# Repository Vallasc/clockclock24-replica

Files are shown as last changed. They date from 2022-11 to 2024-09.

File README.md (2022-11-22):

# ClockClock 24 Replica
This is my personal implementation of the "ClockClock 24" by [Humans Since 1982](https://www.humanssince1982.com/).

<div align="center">
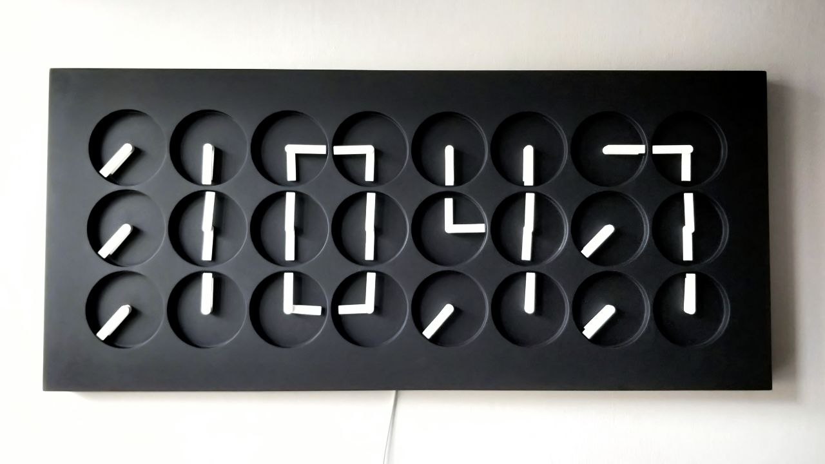
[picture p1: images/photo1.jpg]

</div>

| DISCLAIMER: All files in this repository are intended for personal use only. All design rights go to [Humans Since 1982](https://www.humanssince1982.com/).|
| - |

Clockclock is a kinetic sculpture design by Humans Since 1982, consisting of 24 clocks which by animating show the time in digital format. My attempt to create a replica started by designing the PCB and the case that houses them, and then writing the software to drive the clocks.

---

### Table of Contents: 
1. [Hardware](#hardware)
    1. [Motor](#motor)
    2. [Microcontroller](#microcontroller)
    3. [PCB](#pcb)
2. [Software](#software)
    1. [Master](#master)
    2. [Slave](#slave)
    3. [Web Interface](#web-interface)
    4. [Hands calibration](#hands-calibration)
3. [Case and clock's hands](#case-and-clocks-hands)
4. [Final result](#final-result)

---

## Hardware
The entire clock is composed of 24 sub-clocks, arranged on a 8x3 matrix, that are fully independent. A module that contains 3 clocks and can show vertically an half digit has been designed. A total of 8 boards are used to make up the entire clock, nothing prohibits adding more, thus increasing the number of digits.

### Motor
After careful research, *VID28-05* (or *BKA30D-R5*) stepper motor was chosen. It is made by two separate motors that drive the two shafts individually, that is perfect for attaching the hands. Moreover, this type is sold by some vendors (search on Aliexpress) with no endstops and can turn freely.

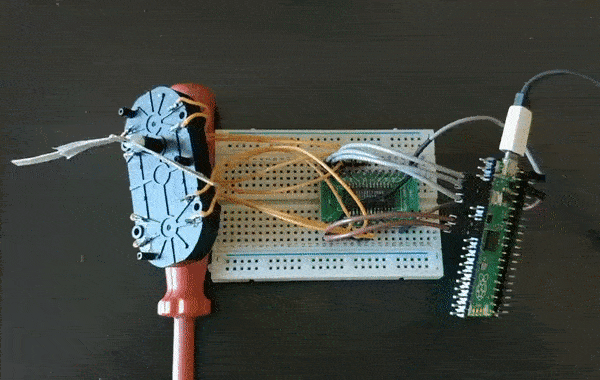
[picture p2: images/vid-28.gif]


These motors are low power and can be runned directly by the microcontroller, but in order not to stress the GPIO a dedicated controller was used. Specifically the *AX1201728SG* (equivalent of *X12.017* and *VID6606* chips) offers advantages over running the motor directly such as uses of microstepping. It requires only two GPIO pins per motor, protects the microprocessor from the inductive effects of the motor coils and requires lower current to be runned by the microcontroller.

### Microcontroller
Two types of microcontrollers are used: **Raspberry-pi-pico** (RP2040) and **ESP8266**. The main reason for this choice is that ESP8266 has wifi capabilities, the design was made before the release of Raspberry-pi-pico-w, now the PCB could be simplified even more. ESP8266 acts as a master and sends commands to the pico boards that run directly the motors. Raspberry-pi-picoIt was chosen because it has a lot of pins, it is reliable and it is available on the market at a relatively low price.

### PCB
The schematic and all the gerber files are placed in the *./pcb* directory. 
<div align="center">
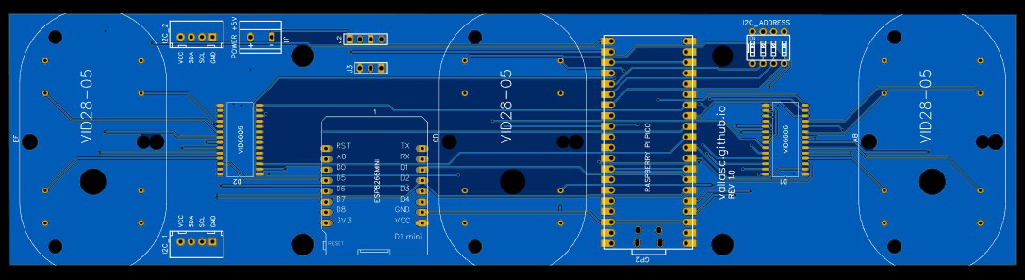
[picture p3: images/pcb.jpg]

</div>

#### Schematic
<div align="center">
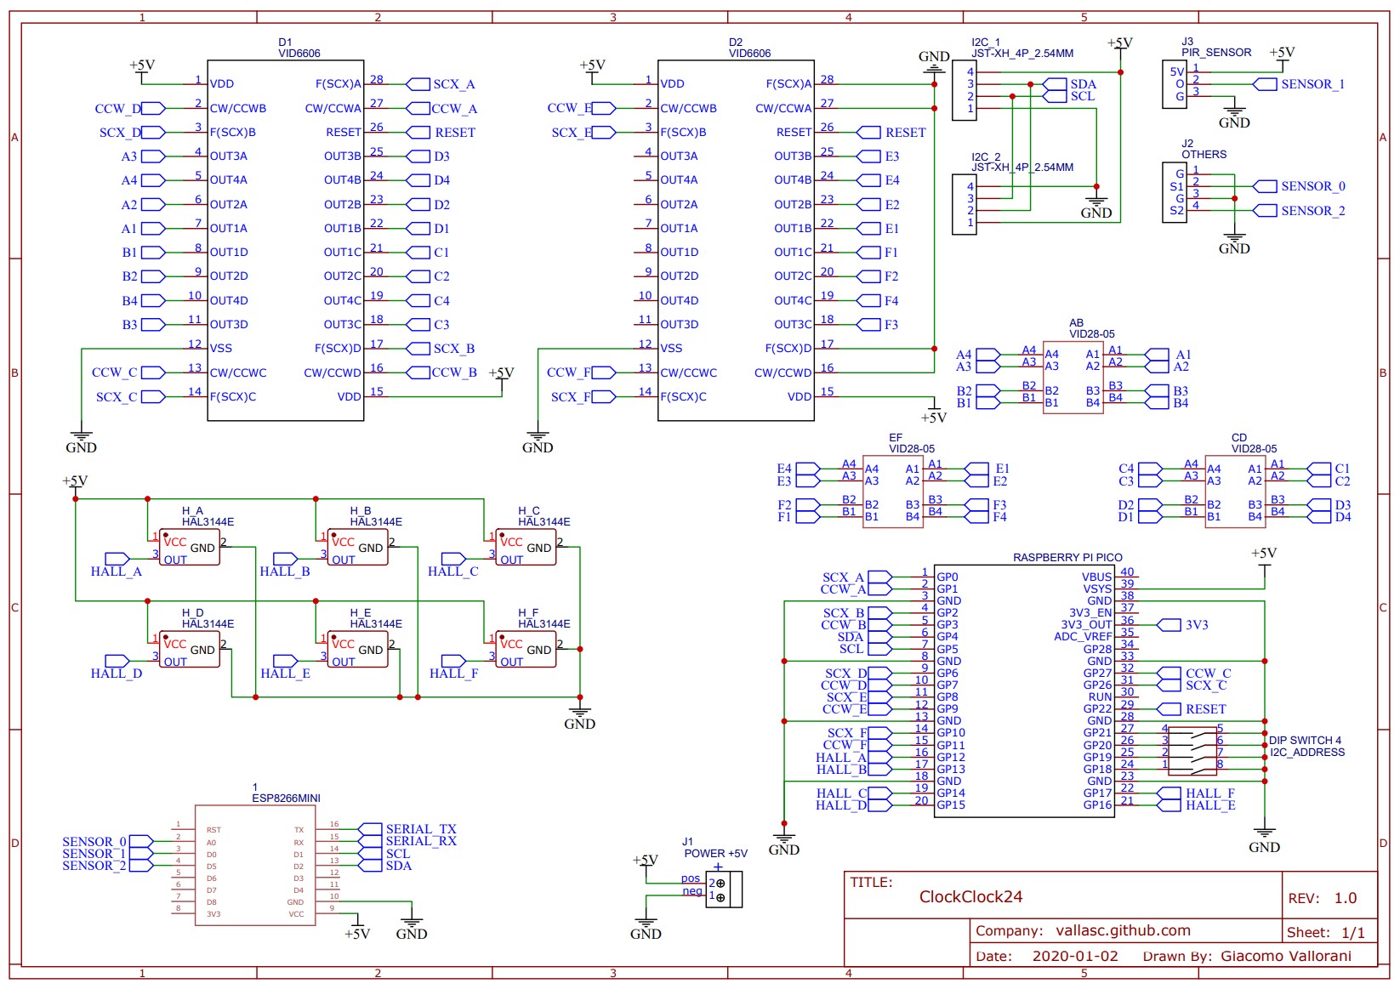
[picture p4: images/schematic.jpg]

</div>
Each board has 2 stepper controllers that in total can run 8 motors. As a design choice, the board has only 3 clocks (6 motors), so 2 outputs are unused. The schematic also contains 6 hall sensors which were to be used to automatically adjust the position of the hands, but in the end they were not added to the final prototype because the magnets were not powerful enough to trigger the sensors. Each board has also housing for ESP8266MINI but it should only be installed on one board (master). This makes it possible to produce only one type of printed circuit board to which components will be soldered according to purpose. Master talks to slaves using I2C protocol, each board is connected to the next in daisy chain. All the boards are powered with 5v and should approximately consume at peak times 1.7 Ah .

#### Bill Of Materials (full clock)
<div align="center">

| Quantity | Name | 
|-|-|
| 8 | PCB board |
| 24 | VID28-05 (or BKA30D-R5) 360 degree mod |
| 16 | AX1201728SG (or VID6606) |
| 8 | Raspberry pi pico |
| 1 | ESP8266 MINI |
| 8 | DIP switch 4 switches |
| 16 | JST XH 2.54 MALE 4 pins |
| 14 | JST XH 2.54 FEMALE 4 pins (for connection cables) |
| 8 | (Optional) power connector |

</div>

---

## Software
On the software side, two different projects were made for master and slave, [PlatformIO](https://platformio.org/)  was used for both of them. The project setup is easy with PlatformIO because it automatically downloads the necessary files. The only parameters you may need to change is *upload_port* and *monitor_port* in *platformio.ini* .

### Slave
The slave code is runned by Raspberry pico, it receives the target hands position through I2C protocol and moves motors accordingly. The I2C address is taken from the position of the 4 switches on the board.

To have a fluid animation, motion must be done using an acceleration curve, so it is used [AccelStepper](http://www.airspayce.com/mikem/arduino/AccelStepper/) library. 
The code is multicore, one core gets bytes from the I2C bus and saves them in the internal buffer, the other core manages to run directly the stepper motors, doing so the animation is not stopped by the I2C interrupts.

### Master
The master code is runned by ESP8266, it is in charge of sending actual hands position to all the boards and to serve the web application.

When powered on, it tries to connect to the configured WiFi network, if it fails then makes an open network. Time synchronization is made, if internet connection is available, using NTP service or it is taken from the client browser that visits the web app. When time changes it sends to the corresponding board the new hands position, the way in which these are to be moved (clockwise, counter clockwise, min distance, max distance, etc.), the speed and the acceleration. In the meantime, it responds to the requests made by the web application made available at http://192.168.1.10 or http://clockclock24.local.

* Animation modes available (for now):
    1. **Lazy**, moves only clock hands that need to be changed by traveling the minimum distance.
    2. **Fun**, moves all the clock's hands in a clockwise direction.
    3. **Waves**, reproduces a domino animation.

### Web interface
On the web application an exact copy of the clock is shown, animations are also cloned and occur at the same time. The interface allows you to change clock mode, set the hours when it should not work and change the wireless connection.

Credits for the clock's web design animation go to [Manuel Wieser](https://manu.ninja/).

<div align="center">
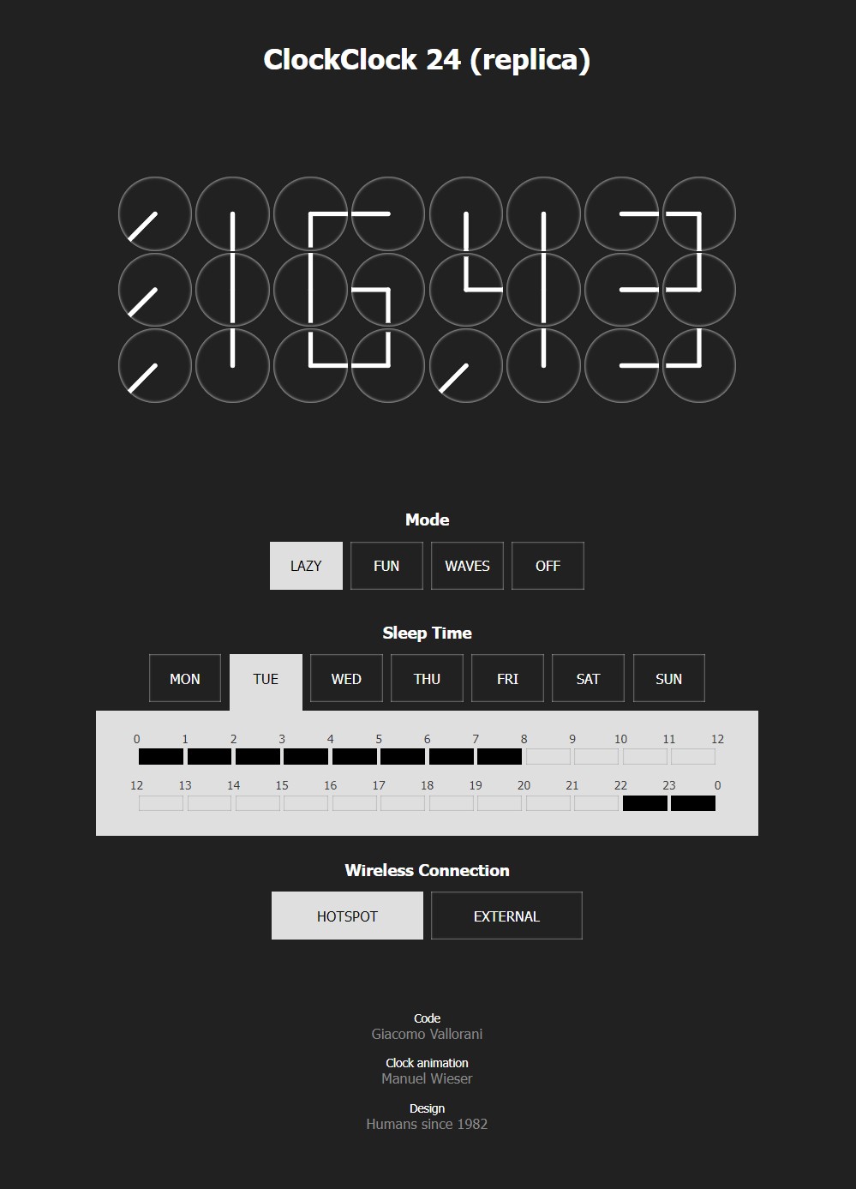
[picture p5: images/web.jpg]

</div>

### Hands calibration
Before powering on the clock, you need to manually set all the clock's hands at 6 o'clock. This process needs to be done every time it is disconnected from power.

---

## Case and clock's hands
The case is one piece, it was made by taking a sheet of black MDF and hollowing out the material with a CNC machine. This gives a lot of stiffness to the structure. The clock's hands are laser cutted from a white plexiglass panel.

Since I don't want to receive a letter from Humans Since 1982’s lawyers, all design files and the actual clock assembly are omitted, more [here](https://hackaday.com/2020/07/31/patent-law-and-the-legality-of-making-something-similar/).
> “Humans Since 1982 have the copyright to works displaying digital time using a grid arrangement of analog clocks…”

---

## Final result
<div align="center">

| Animation type | Result |
| - | - |
| Lazy | sasdasd |
| Fun | sasdasd |
| Waves | sasdasd |

</div>

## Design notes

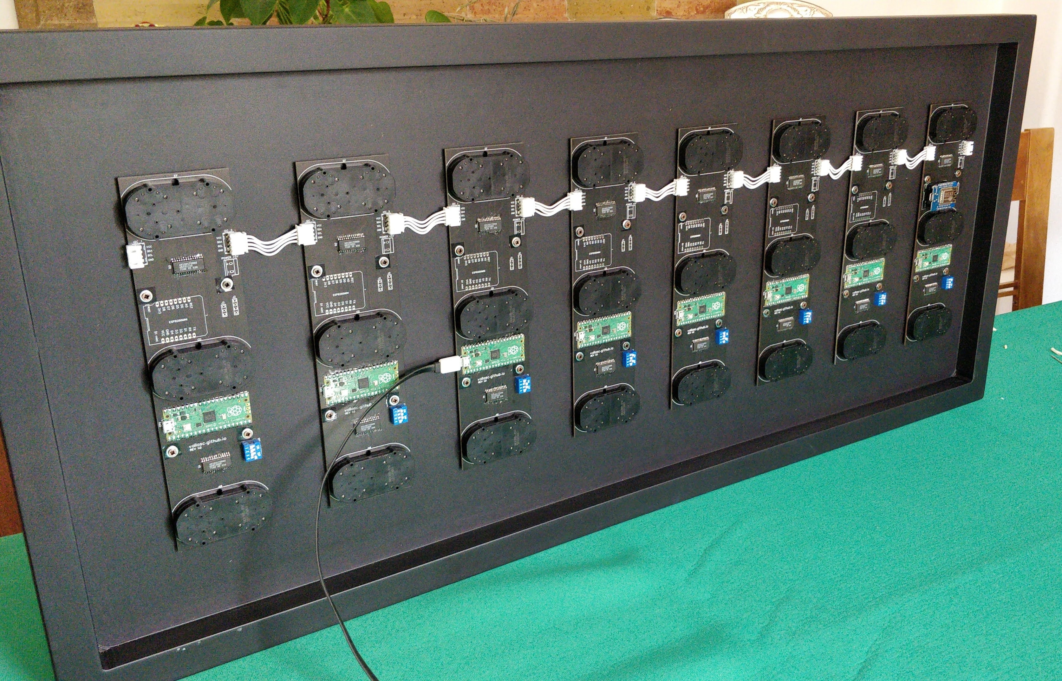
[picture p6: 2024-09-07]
images/IMG-20220928-WA0001.jpeg

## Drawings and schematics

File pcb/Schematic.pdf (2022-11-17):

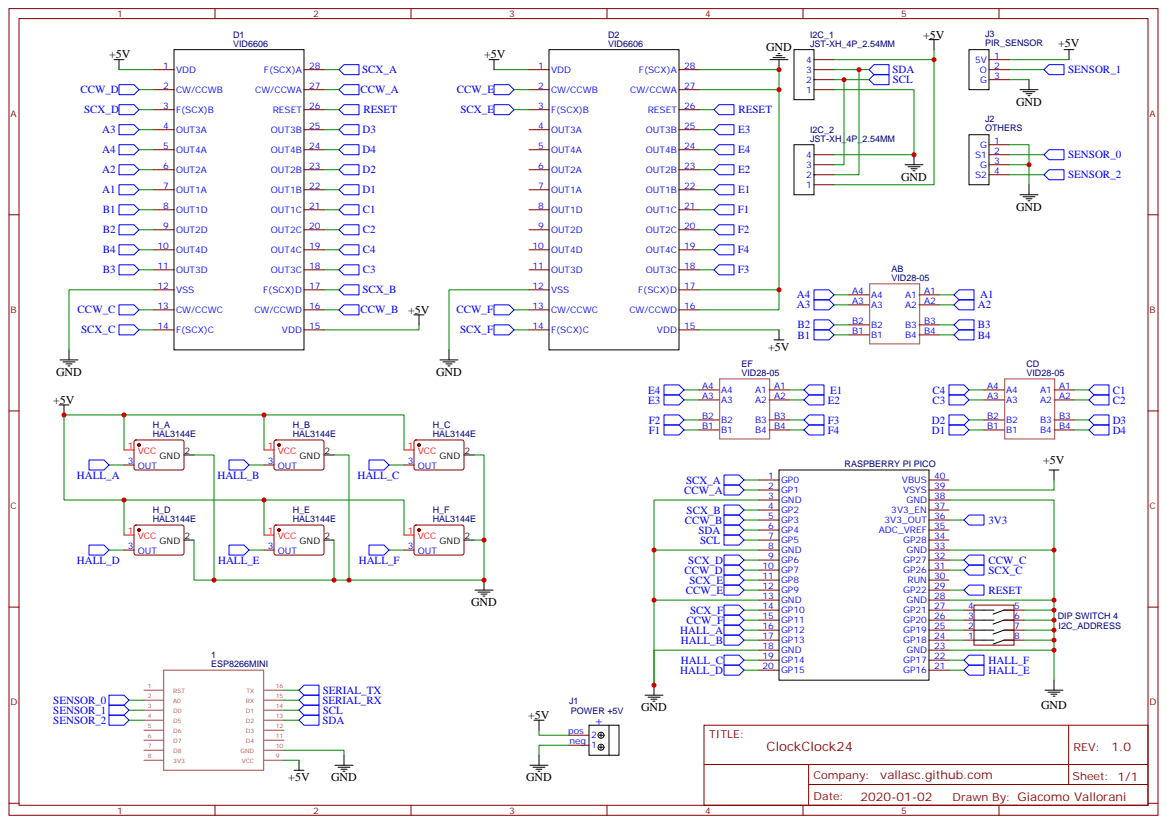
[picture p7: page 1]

Company: vallasc.github.com

Drawn By: Giacomo Vallorani

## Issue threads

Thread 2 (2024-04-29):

Hands turning the incorrect direction.

Kiremas, 2024-04-29:
I finished two PCB's so far which both work but for some reason the hands on some of the steppers turn the wrong way,
which presumably is a fault of the manufacturer of the steppers.

Is there a way to let the slave config know to switch CW and CCW for that particular hand?

Vallasc, 2024-05-03:
It seems that your stepper motors might be connected incorrectly, which is causing them to turn in the wrong direction. You can adjust the direction in which the motors turn by modifying the board [code](https://github.com/Vallasc/clockclock24-replica/blob/a1bb61b2e04a2298400d45447d26f7a0833723cf/slave/src/board.cpp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).

nth1314, 2024-09-06:
> I finished two PCB's so far which both work but for some reason the hands on some of the steppers turn the wrong way, which presumably is a fault of the manufacturer of the steppers.
>
> Is there a way to let the slave config know to switch CW and CCW for that particular hand?

Hi, have you finished this project? Would you like to show me your results? I want to know how to connect the back of it. After I assembled a PCB board, I powered it up but the motor did not work, so I want to know if you have encountered this situation?

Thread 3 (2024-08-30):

VID28-05 (or BKA30D-R5) stepper motor

nth1314, 2024-08-30:
I accidentally saw your work, I like it very much, I want to copy one and put it in the living room, so I would like to know whether the motor you use is unlimited or limited. Can I see the back of this piece of yours? I want to know how it's put together. Although this project has been a long time ago, I hope to get your reply

nth1314, 2024-08-30:
Processing pico (platform: https://github.com/maxgerhardt/platform-raspberrypi.git; board: pico; framework: arduino)
--------------------------------------------------------------------------------------------------------------------------------------------

Verbose mode can be enabled via `-v, --verbose` option
CONFIGURATION: https://docs.platformio.org/page/boards/raspberrypi/pico.html
PLATFORM: Raspberry Pi RP2040 (1.14.0+sha.196d31b) > Raspberry Pi Pico
HARDWARE: RP2040 133MHz, 264KB RAM, 2MB Flash
DEBUG: Current (blackmagic) External (blackmagic, cmsis-dap, jlink, pico-debug, picoprobe, raspberrypi-swd)
PACKAGES:
 - framework-arduinopico @ 1.40001.0+sha.7a9c427
 - tool-mklittlefs-rp2040-earlephilhower @ 5.100300.230216 (10.3.0)
 - tool-openocd-rp2040-earlephilhower @ 5.120300.240125 (12.3.0)
 - tool-rp2040tools @ 1.0.2
 - toolchain-rp2040-earlephilhower @ 5.120300.240125 (12.3.0)
Flash size: 2.00MB
Sketch size: 2.00MB
Filesystem size: 0.00MB
Maximium Sketch size: 2093056 EEPROM start: 0x101ff000 Filesystem start: 0x101ff000 Filesystem end: 0x101ff000
LDF: Library Dependency Finder -> https://bit.ly/configure-pio-ldf
LDF Modes: Finder ~ chain, Compatibility ~ soft
Found 65 compatible libraries
Scanning dependencies...
Dependency Graph
|-- Wire @ 1.0
|-- AccelStepper @ 1.61
Building in release mode
Retrieving maximum program size .pio\build\pico\firmware.elf
Flash size: 2.00MB
Sketch size: 2.00MB
Filesystem size: 0.00MB
Maximium Sketch size: 2093056 EEPROM start: 0x101ff000 Filesystem start: 0x101ff000 Filesystem end: 0x101ff000
Checking size .pio\build\pico\firmware.elf
Advanced Memory Usage is available via "PlatformIO Home > Project Inspect"
RAM:   [          ]   4.0% (used 10592 bytes from 262144 bytes)
Flash: [          ]   3.0% (used 62404 bytes from 2093056 bytes)
Configuring upload protocol...
AVAILABLE: blackmagic, cmsis-dap, jlink, pico-debug, picoprobe, picotool, raspberrypi-swd
CURRENT: upload_protocol = picotool
Looking for upload port...
Using manually specified: COM9
Forcing reset using 1200bps open/close on port COM9
Uploading .pio\build\pico\firmware.elf
rp2040load 1.0.1 - compiled with go1.15.8
.....................
*** [upload] Error 1
======================================================= [FAILED] Took 13.92 seconds =======================================================

 *  终端进程“C:\Users\Administrator\.platformio\penv\Scripts\platformio.exe 'run', '--target', 'upload', '--upload-port', 'COM9'”已终止，退出代码: 1。
 *  终端将被任务重用，按任意键关闭。

 *  正在执行任务: C:\Users\Administrator\.platformio\penv\Scripts\platformio.exe run --target upload --upload-port COM9

Processing pico (platform: https://github.com/maxgerhardt/platform-raspberrypi.git; board: pico; framework: arduino)
--------------------------------------------------------------------------------------------------------------------------------------------

Verbose mode can be enabled via `-v, --verbose` option
CONFIGURATION: https://docs.platformio.org/page/boards/raspberrypi/pico.html
PLATFORM: Raspberry Pi RP2040 (1.14.0+sha.196d31b) > Raspberry Pi Pico
HARDWARE: RP2040 133MHz, 264KB RAM, 2MB Flash
DEBUG: Current (blackmagic) External (blackmagic, cmsis-dap, jlink, pico-debug, picoprobe, raspberrypi-swd)
PACKAGES:
 - framework-arduinopico @ 1.40001.0+sha.7a9c427
 - tool-mklittlefs-rp2040-earlephilhower @ 5.100300.230216 (10.3.0)
 - tool-openocd-rp2040-earlephilhower @ 5.120300.240125 (12.3.0)
 - tool-rp2040tools @ 1.0.2
 - toolchain-rp2040-earlephilhower @ 5.120300.240125 (12.3.0)
Flash size: 2.00MB
Sketch size: 2.00MB
Filesystem size: 0.00MB
Maximium Sketch size: 2093056 EEPROM start: 0x101ff000 Filesystem start: 0x101ff000 Filesystem end: 0x101ff000
LDF: Library Dependency Finder -> https://bit.ly/configure-pio-ldf
LDF Modes: Finder ~ chain, Compatibility ~ soft
Found 65 compatible libraries
Scanning dependencies...
Dependency Graph
|-- Wire @ 1.0
|-- AccelStepper @ 1.61
Building in release mode
Retrieving maximum program size .pio\build\pico\firmware.elf
Flash size: 2.00MB
Sketch size: 2.00MB
Filesystem size: 0.00MB
Maximium Sketch size: 2093056 EEPROM start: 0x101ff000 Filesystem start: 0x101ff000 Filesystem end: 0x101ff000
Checking size .pio\build\pico\firmware.elf
Advanced Memory Usage is available via "PlatformIO Home > Project Inspect"
RAM:   [          ]   4.0% (used 10592 bytes from 262144 bytes)
Flash: [          ]   3.0% (used 62404 bytes from 2093056 bytes)
Configuring upload protocol...
AVAILABLE: blackmagic, cmsis-dap, jlink, pico-debug, picoprobe, picotool, raspberrypi-swd
CURRENT: upload_protocol = picotool
Looking for upload port...
Using manually specified: COM9
Forcing reset using 1200bps open/close on port COM9
Uploading .pio\build\pico\firmware.elf
rp2040load 1.0.1 - compiled with go1.15.8
.....................
*** [upload] Error 1
======================================================= [FAILED] Took 13.72 seconds =======================================================
What causes this?
Hope for your reply

Vallasc, 2024-09-07:
I appreciate your interest in my work! I want to clarify that the motors used in the project are not limited, they can rotate freely 360 degrees.

I have attached images of the mounted boards.
[img1](https://raw.githubusercontent.com/Vallasc/clockclock24-replica/363194655d1605ae0f347418bfaffbc2249db9c9/images/IMG-20220928-WA0001.jpeg)
[img2](https://raw.githubusercontent.com/Vallasc/clockclock24-replica/master/images/IMG_20221118_105347.jpg)

nth1314, 2024-09-07:
Thank you very much for taking time out of your busy schedule to reply to me. I can start to make it now

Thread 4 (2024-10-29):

Testing a single board for functionality.

tomfavell, 2024-10-29:
I am very interested in building your clock design, but I want to take a cautious approach (don't want to end up with 24 clocks I cant use!).
If one were to build a single board as a master, would it be possible to test all the functionality (albeit limited to the last vertical strip of clocks)?
Many thanks
Tom

whosmatt, 2024-11-20:
The master code makes no use of any i2c reads, so it is fully unaware of how many slaves are connected. If you choose one board, you should be able to freely test all columns by changing the address on the DIP switch and power cycling the board.

tomfavell, 2024-11-20:
Thank you MattI have one board working well as you described thanks.I did find that both hands have to be down at 6 o’clock before power up. Otherwise looking good and waiting for parts to build the other 7 boards.I’m thinking of back illuminating the panel as well.Do you know if anyone else has built your design?Tom.    ---- On Wed, 20 Nov 2024 17:22:58 +0000  ***@***.******@***.***> wrote ----
The master code makes no use of any i2c reads, so it is fully unaware of how many slaves are connected. If you choose one board, you should be able to freely test all columns by changing the address on the DIP switch and power cycling the board.

—Reply to this email directly, view it on GitHub, or unsubscribe.You are receiving this because you authored the thread.Message ID: ***@***.***>

whosmatt, 2024-11-20:
This is not my design, I am just building something based on this. I may fork this in the future and make some additions, such as a home position button so you dont need to re initialize all the hands when powering it up. I will share the step files for my clockface design github when I am done designing it.

DerPicknicker, 2025-01-06:
@whosmatt did you made any progress?

tomfavell, 2025-01-07:
Good progress, have everything working, finished case with back light now assembling boards into case.
One thing I cant figure is - I can edit the html code (I want to add some additional controls) but I dont know how this gets compiled into the master file.

whosmatt, 2025-04-03:
My design is complete now, will upload documentation and files to my github soon, probably next week. I am using an MDF 19mm base with 3D printed self-centering spacers and press-fit hands.

DerPicknicker, 2025-04-03:
@whosmatt sounds great. Please share your design. I want such an clock too.

tomfavell, 2025-04-05:
My clock clock has been running now for a few months - no problem

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

DerPicknicker, 2025-04-05:
@tomfavell .. Maybe I am wrong or my program doesn't like your file. It doesn't contain the full holes. Could you maybe share the final design and used material because it looks so Cool with the backlight!

whosmatt, 2025-04-08:
> [@whosmatt](https://github.com/whosmatt) sounds great. Please share your design. I want such an clock too.

https://github.com/whosmatt/clockclock24-replica/

Vallasc, 2025-04-08:
It’s an honor to see so many people reworking and improving my project—thank you all for your enthusiasm and dedication. Unfortunately, my work schedule doesn’t always allow me to respond, but I do read your updates whenever I can. It seems you’re doing a fantastic job even without me, so keep going!

DerPicknicker, 2025-06-10:
@whosmatt ..

What Material would you recommend to use? MDF or do you think real wood would also be possible?

tomfavell, 2025-06-10:
I think rear wood, could look good. It is a large clock so your woodworking skills would need to be good to achieve a high-quality finish.

DerPicknicker, 2025-06-10:
@tomfavell .. thank you for your hint. I will use an CNC. So it's more a question about the material. Which wood type? Which thickness?

Or should I use MDF and put a small wood layer on top. Which will look cheap if you look from the sides.

tomfavell, 2025-06-10:
Go for real solid wood. I used 19mm, its a compromise between the depth of the clock face and the length of the spindle. I cut all the way through and added a 4mm (I think) mdf backing. My CNC wouldn't have given such a smooth finish on the bottom cut.

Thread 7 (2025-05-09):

Clock suddenly stopping

Inny16, 2025-05-09:
Hello,
First of all I want to thank you for this awesome project. I was able to build the clock and made it to work as intended, only issue I'm having is that it works for couple of hours and then it stops (the hands are still sturdy which suggests the motors still receive power) and the time does not change. Sometimes it stops only the 3rd and 4rd digit first and then the rest, sometimes it stops all at once.
Longest time I had it working without stopping was for 2 days. Tried changing several USB power adapters but the issue persists.
Any ideas what could be causing it?
Thank you

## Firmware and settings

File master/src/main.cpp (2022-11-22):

#include <Arduino.h>
#include <Wire.h>
#include <TimeLib.h>

#include "i2c.h"
#include "clock_state.h"
#include "clock_manager.h"
#include "digit.h"
#include "wifi_utils.h"
#include "web_server.h"
#include "clock_config.h"
#include "ntp.h"

int last_hour = -1;
int last_minute = -1;
bool is_stopped = false;

/**
 * Sets clock to the current time
*/
void set_time();

/**
 * Sets clock time using lazy animation
*/
void set_lazy();

/**
 * Sets clock time using fun animation
*/
void set_fun();

/**
 * Sets clock time using waves animation
*/
void set_waves();

/**
 * Sets clock to stop state
*/
void stop();

/**
 * Custom delay to update web clients
 * @param value   time in milliseconds
*/
void _delay(int value);

void setup() {
  Serial.begin(115200);
  Serial.println("\nclockclock24 replica by Vallasc master v1.0");
  delay(3000);
  // Load configuration from EEPROM
  begin_config();

  Wire.begin();
  pinMode(LED_BUILTIN, OUTPUT);

  if(get_connection_mode() == HOTSPOT)
    wifi_create_AP("ClockClock 24", "clockclock24");
  else if( !wifi_connect(get_ssid(), get_password(), "clockclock24") )
  {
    set_connection_mode(HOTSPOT);
    wifi_create_AP("ClockClock 24", "clockclock24");
  }

  if(get_connection_mode() == EXT_CONN)
  {
    // Initialize NTP
    begin_NTP();
    setSyncProvider(get_NTP_time);
    // Sync every 30 minutes
    setSyncInterval(60 * 30);
  }

  // Starts web server
  server_start();
}

void loop() {

  if(get_connection_mode() == HOTSPOT && is_time_changed_browser())
  {
    t_browser_time browser_time = get_browser_time();
    setTime(browser_time.hour, 
      browser_time.minute, 
      browser_time.second, 
      browser_time.day, 
      browser_time.month,  
      browser_time.year);
  }

  if(get_connection_mode() == EXT_CONN && get_timezone() != get_ntp_timezone())
  {
    set_ntp_timezone(get_timezone());
    setSyncProvider(get_NTP_time);
  }

  get_clock_mode() != OFF ? set_time() : stop();

  update_MDNS();
  handle_webclient();
}

void set_time()
{
  int day_week = (weekday() + 5) % 7;
  if(get_sleep_time(day_week, hour()))
    stop();
  else if(hour() != last_hour || minute() != last_minute)
  {
    is_stopped = false;
    last_hour = hour();
    last_minute = minute();
    switch(get_clock_mode())
    {
      case LAZY:
        set_lazy();
        break;
      case FUN:
        set_fun();
        break;
      case WAVES:
        set_waves();
        break;
    }
  }
}

void set_lazy()
{
  set_speed(200);
  set_acceleration(100);
  set_direction(MIN_DISTANCE);
  set_clock_time(last_hour, last_minute);
}

void set_fun()
{
  set_speed(400);
  set_acceleration(150);
  set_direction(CLOCKWISE2);
  set_clock_time(last_hour, last_minute);
}

void set_waves()
{
  set_speed(800);
  set_acceleration(150);
  set_direction(MIN_DISTANCE);
  set_clock(d_IIII);
  _delay(9000);
  set_speed(400);
  set_acceleration(100);
  set_direction(CLOCKWISE2);
  t_full_clock clock = get_clock_state_from_time(last_hour, last_minute);
  for (int i = 0; i <8; i++)
  {
    set_half_digit(i, clock.digit[i/2].halfs[i%2]);
    delay(400);
  }
}

void stop()
{
  if(!is_stopped)
  {
    is_stopped = true;
    last_hour = -1;
    last_minute = -1;
    set_direction(MIN_DISTANCE);
    set_speed(200);
    set_acceleration(100);
    set_clock(d_stop);
  }
}

void _delay(int value)
{
  for (int i = 0; i <value/100; i++)
  {
    update_MDNS();
    handle_webclient();
    delay(value/100);
  }
}

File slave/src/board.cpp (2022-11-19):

#include "board.h"

// Define a stepper and the pins it will use
ClockAccelStepper _motors[6] = {
  ClockAccelStepper(ClockAccelStepper::DRIVER, F_STEP, F_DIR), // 0 -> h clock 0
  ClockAccelStepper(ClockAccelStepper::DRIVER, E_STEP, E_DIR), // 1 -> m clock 0
  ClockAccelStepper(ClockAccelStepper::DRIVER, D_STEP, D_DIR), // 2 -> h clock 1
  ClockAccelStepper(ClockAccelStepper::DRIVER, C_STEP, C_DIR), // 3 -> m clock 1
  ClockAccelStepper(ClockAccelStepper::DRIVER, B_STEP, B_DIR), // 4 -> h clock 2
  ClockAccelStepper(ClockAccelStepper::DRIVER, A_STEP, A_DIR)  // 5 -> m clock 2
};

uint8_t _i2c_address = 0;

static int sanitize_angle(int angle)
{
  angle = angle % 360;
  return angle < 0 ? 360 + angle : angle;
}

void board_begin()
{
  // Reset motor controllers
  pinMode(RESET, OUTPUT);
  digitalWrite(RESET, HIGH);

  // Init motors
  for(int i = 0; i < 6; i++)
  {
    if(i % 2 == 1)
      _motors[i].setReverse(true);
    _motors[i].setMaxMotorSteps(STEPS);
    _motors[i].setHandAngle(INIT_HANDS_ANGLE);
    _motors[i].setMinPulseWidth(0);
  }

  pinMode(ADDR_1, INPUT_PULLUP);
  pinMode(ADDR_2, INPUT_PULLUP);
  pinMode(ADDR_3, INPUT_PULLUP);
  pinMode(ADDR_4, INPUT_PULLUP);
  _i2c_address = !digitalRead(ADDR_1) + 
               (!digitalRead(ADDR_2) << 1) + 
               (!digitalRead(ADDR_3) << 2) + 
               (!digitalRead(ADDR_4) << 3);
}

void board_loop()
{
  for(int i = 0; i < 6; i++)
    _motors[i].run();
}

uint8_t get_i2c_address()
{
  return _i2c_address;
}

bool clock_is_running(int index)
{
  if( index < 0 || index > 2)
    return false;

  return _motors[index*2].distanceToGo() != 0 || 
         _motors[index*2 + 1].distanceToGo();
}

void set_clock(int index, t_clock state)
{
  int angle_h = sanitize_angle(state.angle_h + state.adjust_h);
  _motors[index*2].setMaxSpeed(state.speed_h);
  _motors[index*2].setAcceleration(state.accel_h);
  _motors[index*2].moveToAngle(angle_h, state.mode_h);

  int angle_m = sanitize_angle(state.angle_m + state.adjust_m);
  _motors[index*2 + 1].setMaxSpeed(state.speed_m);
  _motors[index*2 + 1].setAcceleration(state.accel_m);
  _motors[index*2 + 1].moveToAngle(angle_m, state.mode_m);
}

void adjust_h_hand(int index, signed char amount)
{
  int steps = amount * STEPS / 360;
  _motors[index*2 + 1].move(steps);
  _motors[index*2 + 1].runToPosition();
}

void adjust_m_hand(int index, signed char amount)
{
  int steps = amount * STEPS / 360;
  _motors[index*2].move(-steps);
  _motors[index*2].runToPosition();
}

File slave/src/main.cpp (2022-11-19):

#include <Wire.h>

#include "board_config.h"
#include "board.h"
#include "clock_state.h"
#include "i2c.h"

const t_clock default_clock = {0, 0, 0, 0, 0, 0, 0, 0, 0, 0};

// int spin_num; //The spin lock number
spin_lock_t *spin_lock[3]; //The spinlock object that will be associated with spin_num

t_half_digit target_clocks_state;
t_half_digit current_clocks_state;

// I2C runs on main core (core 0)
void receiveEvent(int how_many)
{
  // Serial.println("Received something");
  if (how_many >= sizeof(half_digit))
  {
    t_half_digit tmp_state;
    I2C_readAnything (tmp_state);

    for (uint8_t i = 0; i < 3; i++)
    {
      spin_lock_unsafe_blocking(spin_lock[i]); //Acquire the spin lock without disabling interrupts
      target_clocks_state.clocks[i] = tmp_state.clocks[i];
      target_clocks_state.change_counter[i] = tmp_state.change_counter[i];
      spin_unlock_unsafe(spin_lock[i]); //Release the spin lock without re-enabling interrupts
    }
  }
}

void setup()
{  
  Serial.begin(115200);
  Serial.println("clockclock24 replica by Vallasc slave v1.0");

  board_begin();
  target_clocks_state = {{default_clock, default_clock, default_clock}, {0, 0, 0}};

  for (uint8_t i = 0; i < 3; i++)
  {
    int spin_num = spin_lock_claim_unused(true); //Claim a free spin lock. If true the function will panic if none are available
    spin_lock[i] = spin_lock_init(spin_num); //Initialise a spin lock
  }

  Wire.begin(get_i2c_address());
  Wire.onReceive(receiveEvent);
}

void loop()
{
  delay(10);
}

void setup1() 
{
  current_clocks_state = {{default_clock, default_clock, default_clock}, {0, 0, 0}};
}

// Steppers on core 1
void loop1()
{
  board_loop();
  for (uint8_t i = 0; i < 3; i++)
  {
    if(!clock_is_running(i) && current_clocks_state.change_counter[i] != target_clocks_state.change_counter[i])
    {
      //Serial.printf("Inside clock %d\n", i);
      spin_lock_unsafe_blocking(spin_lock[i]);
      current_clocks_state.clocks[i] = target_clocks_state.clocks[i];
      current_clocks_state.change_counter[i] = target_clocks_state.change_counter[i];
      spin_unlock_unsafe(spin_lock[i]);

      if(current_clocks_state.clocks[i].mode_h == ADJUST_HAND)
        adjust_h_hand(i, current_clocks_state.clocks[i].adjust_h);

      if(current_clocks_state.clocks[i].mode_m == ADJUST_HAND)
        adjust_m_hand(i, current_clocks_state.clocks[i].adjust_m);

      if(current_clocks_state.clocks[i].mode_h <= MAX_DISTANCE3)
        set_clock(i, current_clocks_state.clocks[i]);
    }
  }
}

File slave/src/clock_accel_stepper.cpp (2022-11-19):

#include "clock_accel_stepper.h"

ClockAccelStepper::ClockAccelStepper(uint8_t interface, uint8_t pin1, uint8_t pin2, uint8_t pin3, uint8_t pin4, bool enable)
    : AccelStepper(interface, pin1, pin2, pin3, pin4, enable)
{
  _current_angle = 0;
  _reverse = false;
}

void ClockAccelStepper::setHandAngle(int angle)
{
  _current_angle = angle;
}

void ClockAccelStepper::setReverse(bool reverse)
{
  _reverse = reverse;
}

void ClockAccelStepper::setMaxMotorSteps(int steps)
{
  _max_steps = steps;
}

int ClockAccelStepper::calcAngleClockwise(int current_angle, int target_angle)
{
  int delta = (target_angle - current_angle) % 360;
  return (delta <= 0) ? -delta : 360 - delta;
}

int ClockAccelStepper::calcAngleCounterclockwise(int current_angle, int target_angle)
{
  int delta = (target_angle - current_angle) % 360;
  return (delta < 0) ? 360 + delta : delta;
}

void ClockAccelStepper::moveToAngle(int angle, int direction)
{
  int multiplier = 1;
  int delta;

  if (direction <= CLOCKWISE3) // CLOCKWISE
  {
    delta = calcAngleClockwise(_current_angle, angle);
    multiplier = direction;
  }
  else if (direction <= COUNTERCLOCKWISE3) // COUNTERCLOCKWISE
  {
    delta = calcAngleCounterclockwise(_current_angle, angle);
    multiplier = direction - 3;
  }
  else if (direction <= MIN_DISTANCE3) // MIN_DISTANCE
  {
    multiplier = direction - 6;
    int delta1 = calcAngleClockwise(_current_angle, angle);
    int delta2 = calcAngleCounterclockwise(_current_angle, angle);
    direction = delta1 < delta2 ? CLOCKWISE : COUNTERCLOCKWISE; // if == COUNTERCLOCKWISE
    delta = delta1 < delta2 ? delta1 : delta2;
  }
  else if (direction <= MAX_DISTANCE3)
  {
    multiplier = direction - 9;
    int delta1 = calcAngleClockwise(_current_angle, angle);
    int delta2 = calcAngleCounterclockwise(_current_angle, angle);
    direction = delta1 > delta2 ? CLOCKWISE : COUNTERCLOCKWISE; // if == COUNTERCLOCKWISE
    delta = delta1 > delta2 ? delta1 : delta2;
  }

  _current_angle = angle;
  int steps = delta * _max_steps / 360;

  if (direction <= CLOCKWISE3) // CLOCKWISE
    steps = steps + (_max_steps * multiplier);
  else if (direction <= COUNTERCLOCKWISE3) // COUNTERCLOCKWISE
    steps = (steps + (_max_steps * multiplier)) * -1;

  move(steps * (_reverse ? -1 : 1));
}

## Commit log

2022-11-10 Update arduino core
2022-11-10 Add board config manager
2022-11-11 Update board test
2022-11-17 Add pcb
    [Drill_NPTH_Through.DRL, Drill_PTH_Through.DRL, Drill_PTH_Through_Via.DRL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]
2022-11-22 Fix bug no connection switch
    [main.cpp, web_server.cpp]
